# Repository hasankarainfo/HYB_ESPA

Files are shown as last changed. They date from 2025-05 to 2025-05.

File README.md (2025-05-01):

# HYB_ESPA CNC CONTROLLER BOARD
4 Adet Step motor bağlanabilir CNC kontrol kartı.

<p align="center">
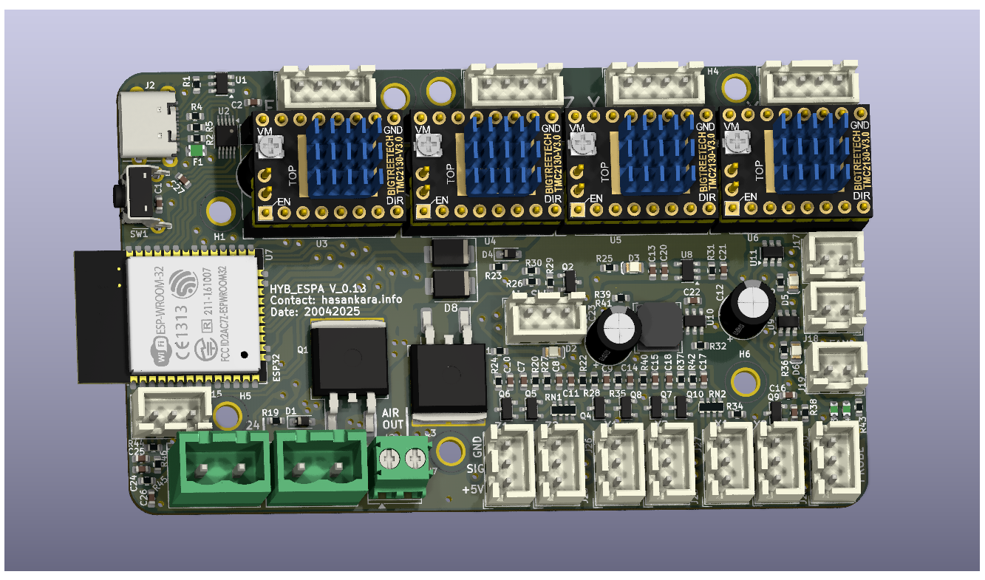
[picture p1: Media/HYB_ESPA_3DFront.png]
HYB_ESPA CNC Controller Board Readme
    
</p>
<p align="center"> Tasarım Ön Görünüm</p>
<p align="center">   
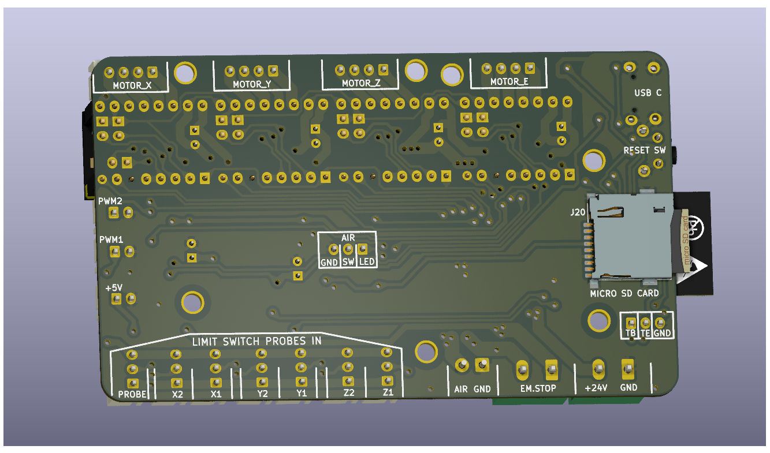
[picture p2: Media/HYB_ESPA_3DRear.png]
HYB_ESPA CNC Controller Board Readme
    
</p>
<p align="center"> Tasarım Arka Görünüm </p>

### ESP32 ile tasarlanmış cnc kontrolcü kartlarına genel bakış;

Temelde donanımsal olarak iki farklı yapıda görmek mümkün. 
İlki daha sade olan (ESPA), doğrudan mcu pinleri ile çevresel bileşen bağlantılandırılmış. 
İkincisi ise (ESPE), bazı bileşenlerin çıkış gpio ihtiyaçları için hc595 entegreleri kullanılıyor olması.

FYSETC_E4, Hem marlin hem fluidnc hem grbl firmware yazılımlarıyla uyumlu hemde açık kaynak paylaşılan projeden şematik olarak faydalanmak mümkün.
Altium ile geliştirilen proje açık kaynak paylaşılmıştır. 4 Adet TMC2209 dahili olarak step sürücüleri üzerinde barındırıyor. 
Sürücü uart bağlantıları ve uart donanımsal adreslemesini kullanmaktadır.

MKS-TinyBee, firmware yazılımları ile yine fazlaca uyumlu, yalnız kaynak tasarım olarak açık da yalnızca pdf bulunuyor. GPIO genişleme yapısı kullanılıyor. 
5 adet motor sürücü için 2* dip-8 header standart pololu breakout yapısı kullanılarak esnek motor sürücü bağlantı seçeneği sunmakta. 
yalnız TMC2208 ve ..09 için uart bağlantısı göz ardı edilmiş. Step sürücü header pinlerindeki RST ve SLP pinleri doğrudan kısa devre edili olmaktadır.

MRR_ESPE kicad ile tasarlanmış ve açık kaynak olarak paylaşılmış, tinybee ile yapısal olarak ve mcu pin görevleri olarak fazlaca benzerliği bulunan bir proje.
ek olarak SPI uyumlu step sürücüler ile haberleşmeli kullanılabilmesi için jumper seçenekleri sunmakta. 

Step sürücü header pinlerindeki MS1, MS2, MS3, RST jumper ile kontrol edilebilirken RST ve SLP pinleri de hem jumper ile kısa devre yapılaibliyor hemde kısa devre kaldırılıp mcu ya bağlanabiliyor. Özellikle TMC2208 ve ..09 uart haberleşmesi için MS3->TX ve SLP->RX olarak kullanılabileceği için gerekli esneklikler sağlanmış olmakta. 

MRR_ESPA ise yine açık kaynak paylaşılmış gpio genişleme kullanılmayan versiyonu olarak düşünülebilir.

Uart haberleşmeli step motor sürücüleri, çoğu kontrolcüye etkili düzeyde avantaj sağlamaktadır. 
Her sürücü Uart haberleşmesi için ayrıca mcu ya bağlamak fazlaca gpio kullanımı gerektirebilir.
ESP32 nin kısıtlı pin durumu için bu bir problem haline gelir. Bu sebeple Tek bir sürücüyü hem rx hem tx ile mcu bağlayıp, tüm sürücülerin sadece rx pinlerini paralel bağlamak kısmen çözüm olabiliyor.

Toplamda 2 pin gpio kullanılarak tüm sürücülere komut gönderimi mümkün olabiliyor, özellikle mod geçişleri, eşik değerleri, akım limiti microstep gibi değerlerin güncellenmesi mümkün olur.
TMC2209 uart adresleme özelliği bulunur iken TMC2208 bu özelliği desteklemez ve adres farketmeksizin tüm komutlara geri bildirim göndermektedir.
TMC2209 step motor limit switch özelliği barındırır, TMC2208 bu özellik yine bulunmamaktadır.
TMC2209 Uart adreslemesi için MS1 ve MS2 pinlerini kullanır, farklı adreslenerek uart bağlantısı paralellenmiş TMC2209 sürücüleri ile birebir haberleşme mümkün olur. 

Tek uart bağlantısı ile çoklu TMC2208 haberleşmesi kısmen mümkün olabilmektedir. Sürücülerin hepsi rx özelliği aktif iken, yalnızca birisi tx yapabilecek donanım yapısı kurgulandığında tüm sürücülere aynı parametre yükleme başarılı olmaktadır.

Açık kaynak paylaşımlar incelendiğinde esnek ve sade yapısı ile FYSETC_E4 projesi dikkat çekmektedir. 

Kendi tasarımımızı şekillendirirken özellikle gpio numara görev atamalarında ve step motor sürücü sayısında FYSETC_E4 esinlenmiş olduk.

### Tasarıma ilişkin;
1. Step motor sürücüleri pololu breakout pin yapısına uyumlu tasarlanarak, farklı step motor sürücülerine uyumluluk sağlandı. 
2. TMC2208 sürücüleri ile kullanıldığında uart üzerinden parametre yüklenebilir iken, TMC2209 ile UART RX-TX jumper takılarak, ve sürücülerde MS1, MS2 jumper configurasyonu ile uart adreslemeli kullanılabilirlik sağlandı.
3. +24V giriş voltajı ve P-mos yapısında ters bağlantı koruma özelliği eklendi.
4. Air out çıkışı ile, 42A akım değerinde ki P-mos ile Denetleyiciden kontrol edilen güçlü bir çıkış elde edildi. 24V ile beslenen lazer yada spindle doğrudan bu terminalden beslenebilir.
5. Emergency Switch terminal ile, step motor beslemesi ve Air out çıkışı, kontrolcüden bağımsız olarak kesilebilir. Kontrolcü beslemesi ve 5V hattı enerjisi aktif devam eder.
6. 5V fan çıkışı, USB ve LimitSwitch enerji hatları bağımsız PTC sigortaları ile akım korumaları eklendi.
7. Limit switch girişleri x,y ve z eksenleri için çiftlendi, aynı eksene iki farklı limit switch eklenebilir. Limit switch bağlantısı koparsa algılayabilir. Kullanılmayan giriş gnd jumper bağlanmalıdır.
8. Boot için kullanılan gpio 0 Probe bağlantısı için de kullanılmaya başlandı. ESP32 e kod atmak için Probe pini 5v jumperda iken kart resetlenerek başlatılmalıdır.
9. Tasarım aracı olarak Kicad 9 kullanıldı.

###  Layout tarafında;
1. Arduino mega2560 fiziksel boyutlarından esinlenerek 60x100 mm^2 ile alternatif cnc kontrolcü kartlarına kıyasla daha küçük ve sade yapıda tasarlandı.
2. Çift yüz tasarım yapılırken, yalnız 0.8mm delikli vialar kullanıldı. THT komponentler yalnızca arka katmandan bağlantılandı. 
3. Komponentlerin altında via bırakılmayarak kendin yap pcb üretim teknikleri ile üretim mümkün kılındı.
4. 40x40 fan doğrudan pcb üzerine distanslar ile sabitlenebilecek şekilde M3 vida delikleri yerleştirildi.

### ÜRETİM
Profesyonel pcb üretimi için; Plot klasörü içerisinde gerber ve drill dosyaları oluşturuldu.

Kendin yap seçeneği ile pcb üretimi için;
1. Plot_DIY klasörü içerisinde pcb delim için 0.8, 0.9, 1.2, 1.4, 3 mm kalınlıklarında matkap uçlarında farklı gcode lar oluşturuldu.
2. PCB komponent lehimleme işlemi için, F_Paste lazer kesim dosyası ayrıca oluşturuldu. Standart etiket kağıdına kesim yapılabilmektedir.
3. Ön yüz ve Arka yüz lazer kazıma ve hizalaması için gerekli dosyalar oluşturuldu.
4. ESP32 montajlanırken kullanılmayan pinler kapton bant ile izolasyon sağlanmalıdır.
5. ibom klasörü içerisinde html uzantılı web browser da görüntülemek üzere bom dosyası oluşturuldu. Komponent yerleşim ve dizgisinde kullanılabilmektedir.
6. Tüm lazer cnc üretim dosyaları 30W optik gücünde ki lazer makinasına göre kurgulanmıştır. Güç oranlaması ile farklı güçte ki lazer makinalarına uygunlaştırılabilir.

### 0.1b versiyon kendin yap teknikleri ile üretilmiş prototiplere ilişkin görseller
<p align="center">   
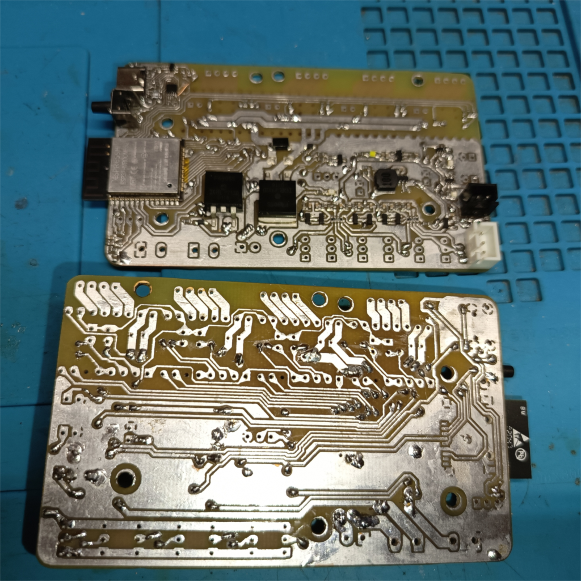
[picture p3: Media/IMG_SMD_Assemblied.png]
    
</p>
<p align="center">SMD Dizgili Ön ve Arka Görünüm </p>

<p align="center">   
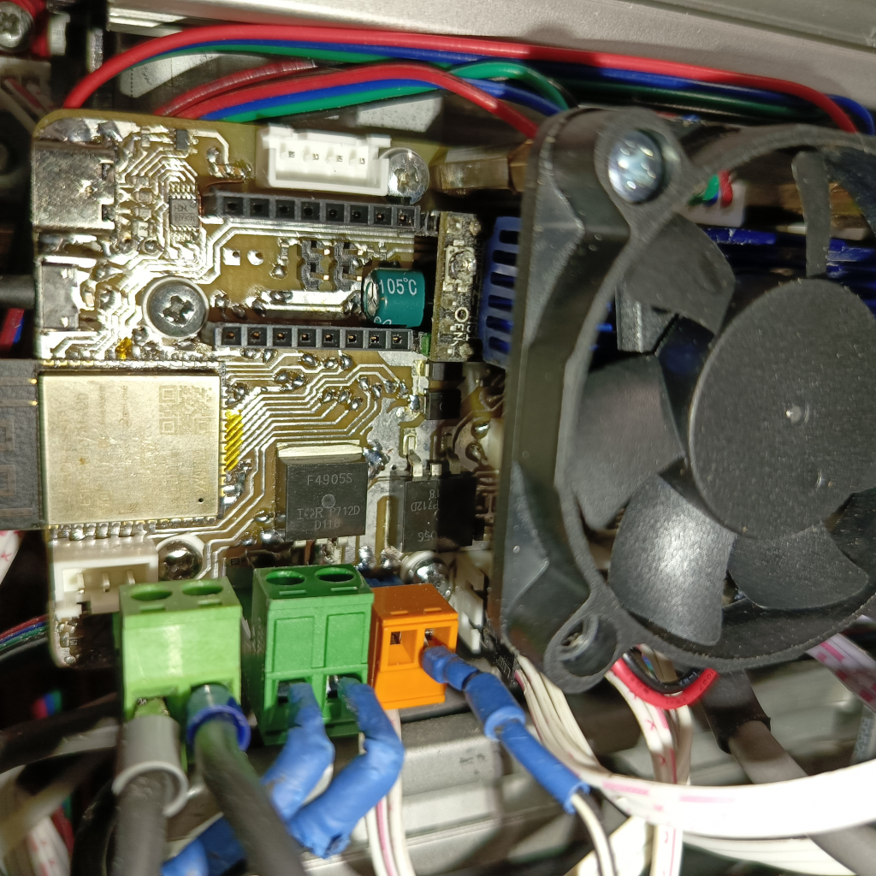
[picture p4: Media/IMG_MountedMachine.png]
    
</p>
<p align="center">Tam Dizgili ve Makine Montajlanmış Görünüm </p>

İlk prototipleme ile birlikte küçük çaplı düzeltmeler tasarımda ve üretim dosyalarında güncellenmiş (v0.1) haldedir.

Bom list oluşturulurken Türkiye piyasasından temin edilmek üzere ürün linkleri oluşturuldu. Yalnız CH340E IC yerli piyasada bulunamadı. 
Belirtilen fiyat bilgileri için ise, vergiler dahil edildi, güncel dolar kuru esas alındı ve dolara çevrildi.

### Bazı testlere ilişkin;
1. Firmware olarak fluidnc v3.9.4 yüklendi. Kontrolcüyle uyumlu, oluşturulan config.yaml dosyası "Settings/" dizini içerisine yerleştirildi.
2. X, Y ve Z eksenleri için 3 adet TMC2208 step motor sürücüleri bağlandı. Tüm sürücülere parametre yükleme yapılabildiği teyit edildi.
3. Arayüz olarak UGS (version 2.1.12) ile bağlanarak temel testler başarıyla sağlandı. 
4. Fiziksel SD kart takılarak web arayüz üzerinden .gcode yüklendi ve ilgili gcode çalıştırıldı. 
5. AirOut çıkışına fiziksel röle bağlandı ve röle çıkışına spindle 220V beslemesi bağlandı.
6. Fluidnc config ayarlarında AirOut çıkışı pwm enable pini ile ilişkilendirildi. 
7. M3 komutu çalıştırılarak Spindle enerjisi sağlandı, M5 komutu çalıştırıldığında Spindle enerjisi otomatik kesildi.
8. Pwm çıkışı ile spindle motor hız ayarı çalıştırıldı.
9. Kontrolcü spindle için enerji çıkışı sağlarken de acil stop basıldığında, spindle enerjisi doğrudan kesilebildi.
10. Limit switch kablo temassızlığı algılanabildiği görüldü.

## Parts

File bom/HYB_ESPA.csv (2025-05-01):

 | Sourced | Placed | References | Value | Part Number | Part Link | Price | Quantity
1 |  |  | C1, C7, C8, C9, C10, C11, C14, C15, C16, C17, C18, C19 | 1nF | CL10B102KB8NNNC | https://ozdisan.com/Product/Detail/11971/CL10B102KB8NNNC | 0.006 | 12
2 |  |  | C2, C13, C21, C22, C25, C27 | 100nF | CC0603KRX7R9BB104 | https://ozdisan.com/Product/Detail/476015/CC0603KRX7R9BB104 | 0.006 | 6
3 |  |  | C3, C4, C5, C6, C12 | 220uF 25V | TMP221M1EE11M | https://ozdisan.com/Product/Detail/404352/TMP221M1EE11M | 0.06 | 5
4 |  |  | C24, C26 | 2.2uF | CL10A225KQ8NNNC | https://www.ozdisan.com/Product/Detail/401994/CL10A225KQ8NNNC | 0.01 | 2
5 |  |  | C20 | 22uF 6.3V | CL10A226MQ8NRNC | https://ozdisan.com/Product/Detail/431703/CL10A226MQ8NRNC | 0.038 | 1
6 |  |  | C23 | 470uF 10V | PKLH-010V471ME110-T2.5 | https://ozdisan.com/Product/Detail/1046555/PKLH-010V471ME110-T2-5 | 0.05 | 1
7 |  |  | R6, R8, R10, R11, R13, R14, R15, R18, R20, R22, R24, R27, R28, R34, R35, R37, R38, R40, R42 | 10K | 0603SAF1002T5E | https://ozdisan.com/Product/Detail/341790/0603SAF1002T5E | 0.0015 | 19
8 |  |  | R1, R2, R7, R9, R12, R16, R21, R26, R30, R31, R44, R45, R46 | 4.7K | RC0603FR-074K7L | https://ozdisan.com/Product/Detail/494590/RC0603FR-074K7L | 0.0018 | 13
9 |  |  | R19, R23, R29, R32 | 100K | 0603SAF1003T5E | https://ozdisan.com/Product/Detail/339374/0603SAF1003T5E | 0.0015 | 4
10 |  |  | R25, R33, R36 | 1K | 0603SAF1001T5E | https://ozdisan.com/Product/Detail/341789/0603SAF1001T5E | 0.0015 | 3
11 |  |  | R4, R5 | 10R | CQ03SAF100JT5E | https://ozdisan.com/Product/Detail/587941/CQ03SAF100JT5E | 0.002 | 2
12 |  |  | R17 | 100R | 0603SAF1000T5E | https://ozdisan.com/Product/Detail/341784/0603SAF1000T5E | 0.0015 | 1
13 |  |  | R39 | 3K | 0603SAF3001T5E | https://ozdisan.com/Product/Detail/339378/0603SAF3001T5E | 0.0015 | 1
14 |  |  | R41 | 16K | 0603SAF1602T5E | https://ozdisan.com/Product/Detail/359801/0603SAF1602T5E | 0.0015 | 1
15 |  |  | R43 | 0R | 0603SAF0000T5E | https://ozdisan.com/Product/Detail/352049/0603SAF0000T5E | 0.0015 | 1
16 |  |  | L1 | 10uH 2.25A | NR6028-100M | https://ozdisan.com/Product/Detail/529366/NR6028-100M | 0.16 | 1
17 |  |  | D2, D3, D5, D6 | LedAir, Led3V3, LedPWM2, LedPWM | HL-PSC-2012H233W-HF4 | https://ozdisan.com/Product/Detail/490003/HL-PSC-2012H233W-HF4 | 0.024 | 4
18 |  |  | D1, D4 | MM3Z12 | MM3Z12-HT | https://ozdisan.com/Product/Detail/581368/MM3Z12-HT | 0.025 | 2
19 |  |  | D7, D8 | SMBJ26CA | SMBJ26CA-HT | https://ozdisan.com/Product/Detail/503708/SMBJ26CA-HT | 0.1 | 2
20 |  |  | U3, U4, U5, U6 | Stepper Breakout | MSK.STP.01.000018 | https://www.motorobit.com/tmc2209-v20-step-motor-surucusu | 6.4 | 4
21 |  |  | U9, U11 | SN74LVC1T45DBV | SN74LVC1T45DBVT | https://ozdisan.com/Product/Detail/616843/SN74LVC1T45DBVT | 0.7 | 2
22 |  |  | U1 | SMF05CT1G | SMF05CT1G | https://www.ozdisan.com/Product/Detail/575537/SMF05CT1G | 0.18 | 1
23 |  |  | U2 | CH340E | C99652 | https://www.lcsc.com/product-detail/USB-ICs_WCH-Jiangsu-Qin-Heng-CH340E_C99652.html | 0.55 | 1
24 |  |  | U7 | ESP32 | ESP32-WROOM-32UE-N4.ESP | https://www.empastore.com/esp32-wroom-32ue-n4-wifi-bluetooth-modul | 3.45 | 1
25 |  |  | U8 | AP7366 | AP7366EA-33W5-7 | https://www.digikey.com/en/products/detail/diodes-incorporated/AP7366EA-33W5-7/18635685 | 0.138 | 1
26 |  |  | U10 | AP63201 | AP63201WU-7 | https://ozdisan.com/Product/Detail/1060556/AP63201WU-7 | 0.4 | 1
27 |  |  | F3, F4 | 100mA 15V | FSMD010-0603-R | https://ozdisan.com/Product/Detail/470708/FSMD010-0603-R | 0.1 | 2
28 |  |  | F1 | 1.1A 6V | KLM2S110RY | https://ozdisan.com/Product/Detail/490835/KLM2S110RY | 0.085 | 1
29 |  |  | SW1 | SW_Reset | L-KLS7-TS6606-5.0-180 | https://ozdisan.com/Product/Detail/462867/L-KLS7-TS6606-5-0-180 | 0.08 | 1
30 |  |  | Q2, Q4, Q5, Q6, Q7, Q8, Q9, Q10 | PJA3440 | PJA3440_R2_00001 | https://ozdisan.com/Product/Detail/517995/PJA3440R200001 | 0.1 | 8
31 |  |  | Q1, Q3 | IRF4905 | IRF4905STRLPBF | https://ozdisan.com/Product/Detail/612241/IRF4905STRLPBF | 1.3 | 2
32 |  |  | RN1, RN2 | 1K | 4D03WGF1001T5E | https://ozdisan.com/Product/Detail/423589/4D03WGF1001T5E | 0.017 | 2
33 |  |  | J4, J5, J7, J8, J10, J11, J12, J14, J31 | E_J2, E_J1, Z_J1, Z_J2, Y_J1, X_J1, Y_J2, X_J2, UART | DS1069-2MVW6X | https://ozdisan.com/Product/Detail/347994/DS1069-2MVW6X | 0.01 | 9
34 |  |  | J15, J16, J24, J25, J26, J27, J28, J29, J30 | AnIn, AirSW, Z_LIM1, Z_LIM2, Y_LIM1, X_LIM1, Y_LIM2, X_LIM2, Probe | L-KLS1-2.50-03-S | https://ozdisan.com/Product/Detail/456067/L-KLS1-2-50-03-S | 0.018 | 9
35 |  |  | J3, J6, J9, J13 | E_Stepper, Z_Stepper, X_Stepper, Y_Stepper | DS1069-4MVW6X | https://ozdisan.com/Product/Detail/347998/DS1069-4MVW6X | 0.02 | 4
36 |  |  | J17, J18, J19 | PWM2_Drive, 5V FAN | DS1069-2MVW6X | https://ozdisan.com/Product/Detail/347994/DS1069-2MVW6X | 0.01 | 3
37 |  |  | J21, J23 | PowerIn, EmStop | ZB2EDGV-5.08-2P | https://ozdisan.com/Product/Detail/1042573/ZB2EDGV-5-08-2P | 0.045 | 2
38 |  |  | J2 | USB_C | nc | https://robiz.net/typec16pin?search=type-c&description=true | 0.2 | 1
39 |  |  | J20 | Micro_SD_Card_Det1 | 112I-TA01 | https://ozdisan.com/Product/Detail/637838/112I-TA01 | 1 | 1
40 |  |  | J22 | AirOut | 15EDGVC-3.5-02P-12-00AH | https://ozdisan.com/Product/Detail/707708/15EDGVC-3-5-02P-12-00AH | 0.1 | 1

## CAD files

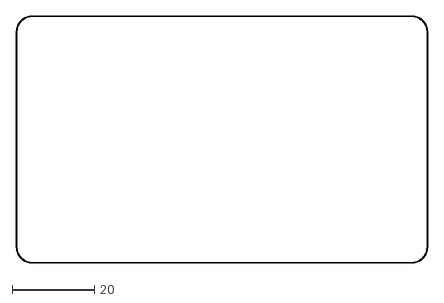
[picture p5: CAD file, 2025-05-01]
Plot_DIY/HYB_ESPA-Edge_Cuts.dxf
100.1 x 60.1

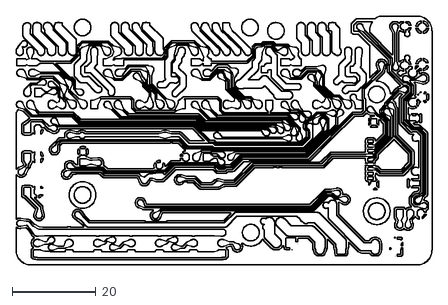
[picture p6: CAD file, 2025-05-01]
Plot_DIY/HYB_ESPA-B_Cu_mirror.DXF
99.4 x 59.4

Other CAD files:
Plot_DIY/HYB_ESPA-F_Paste.dxf

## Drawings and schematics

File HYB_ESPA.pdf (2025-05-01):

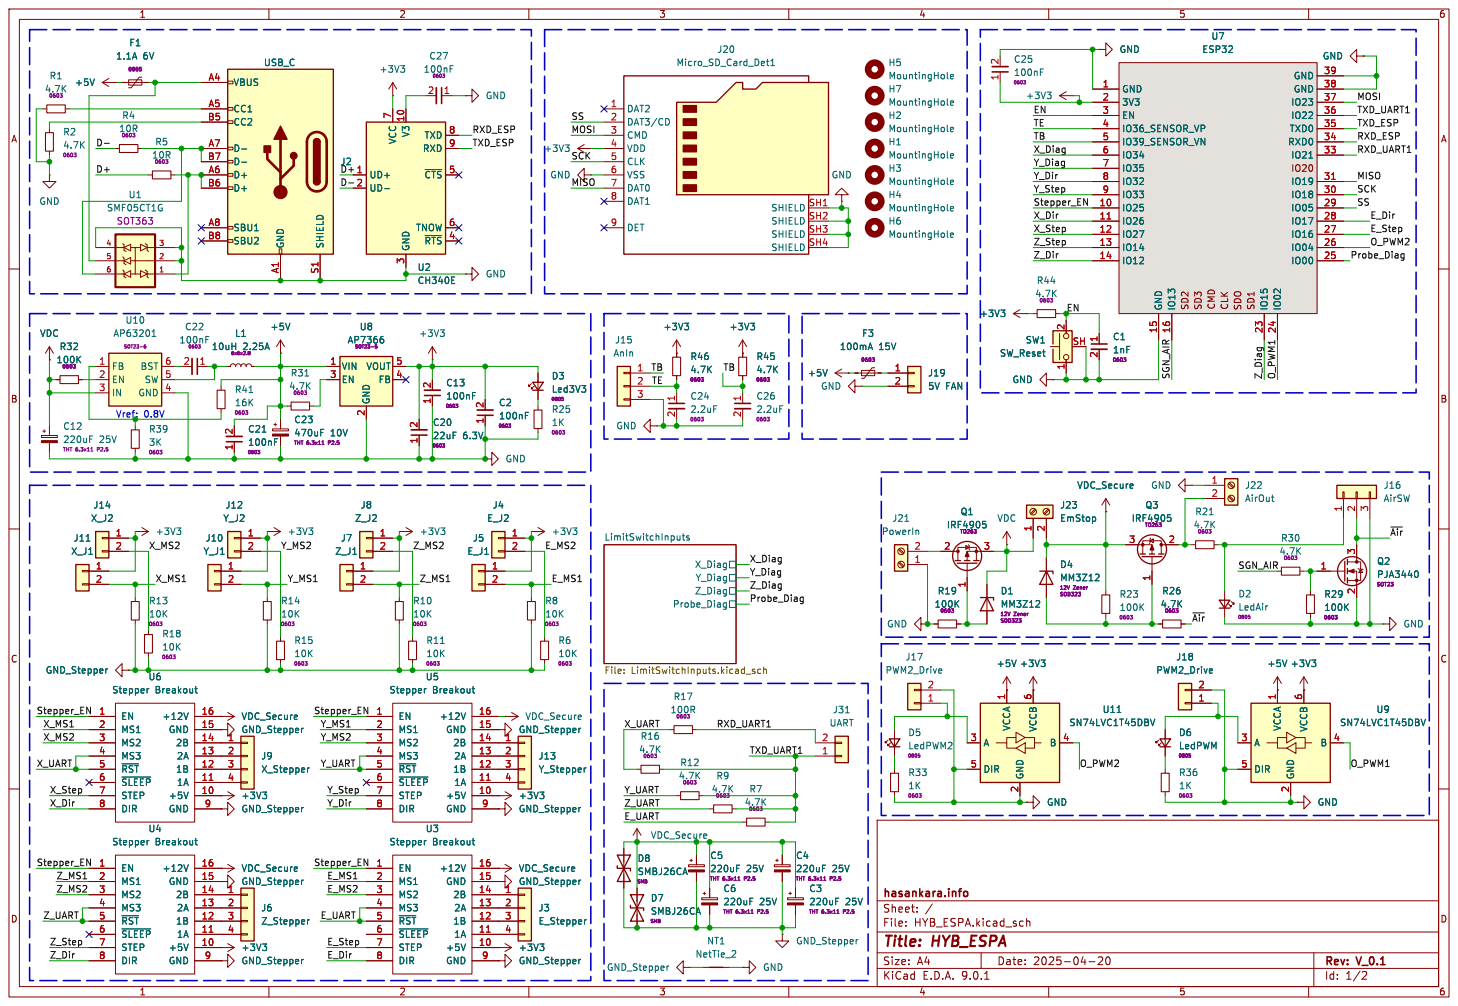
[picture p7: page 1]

3 TXD 8 RXD 9 ~{CTS}5 TNOW 6 ~{RTS}4 U2 CH340E SHIELD S1 GND A1 VBUS A4 CC1 A5 CC2 B5 D- A7 D- B7 D+ A6 D+ B6 SBU1 A8 SBU2 B8

3 TXD 8 RXD 9 ~{CTS}5 TNOW 6 ~{RTS}4

File: HYB_ESPA.kicad_sch Sheet: / hasankara.info

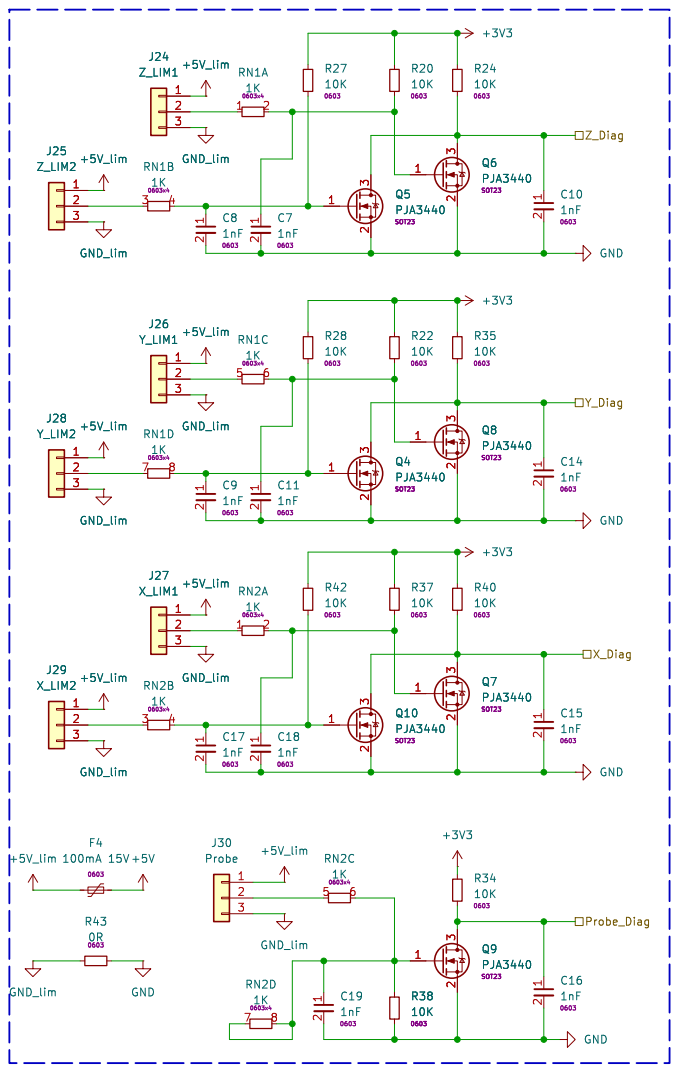
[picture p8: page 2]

File: LimitSwitchInputs.kicad_sch Sheet: /LimitSwitchInputs/ hasankara.info

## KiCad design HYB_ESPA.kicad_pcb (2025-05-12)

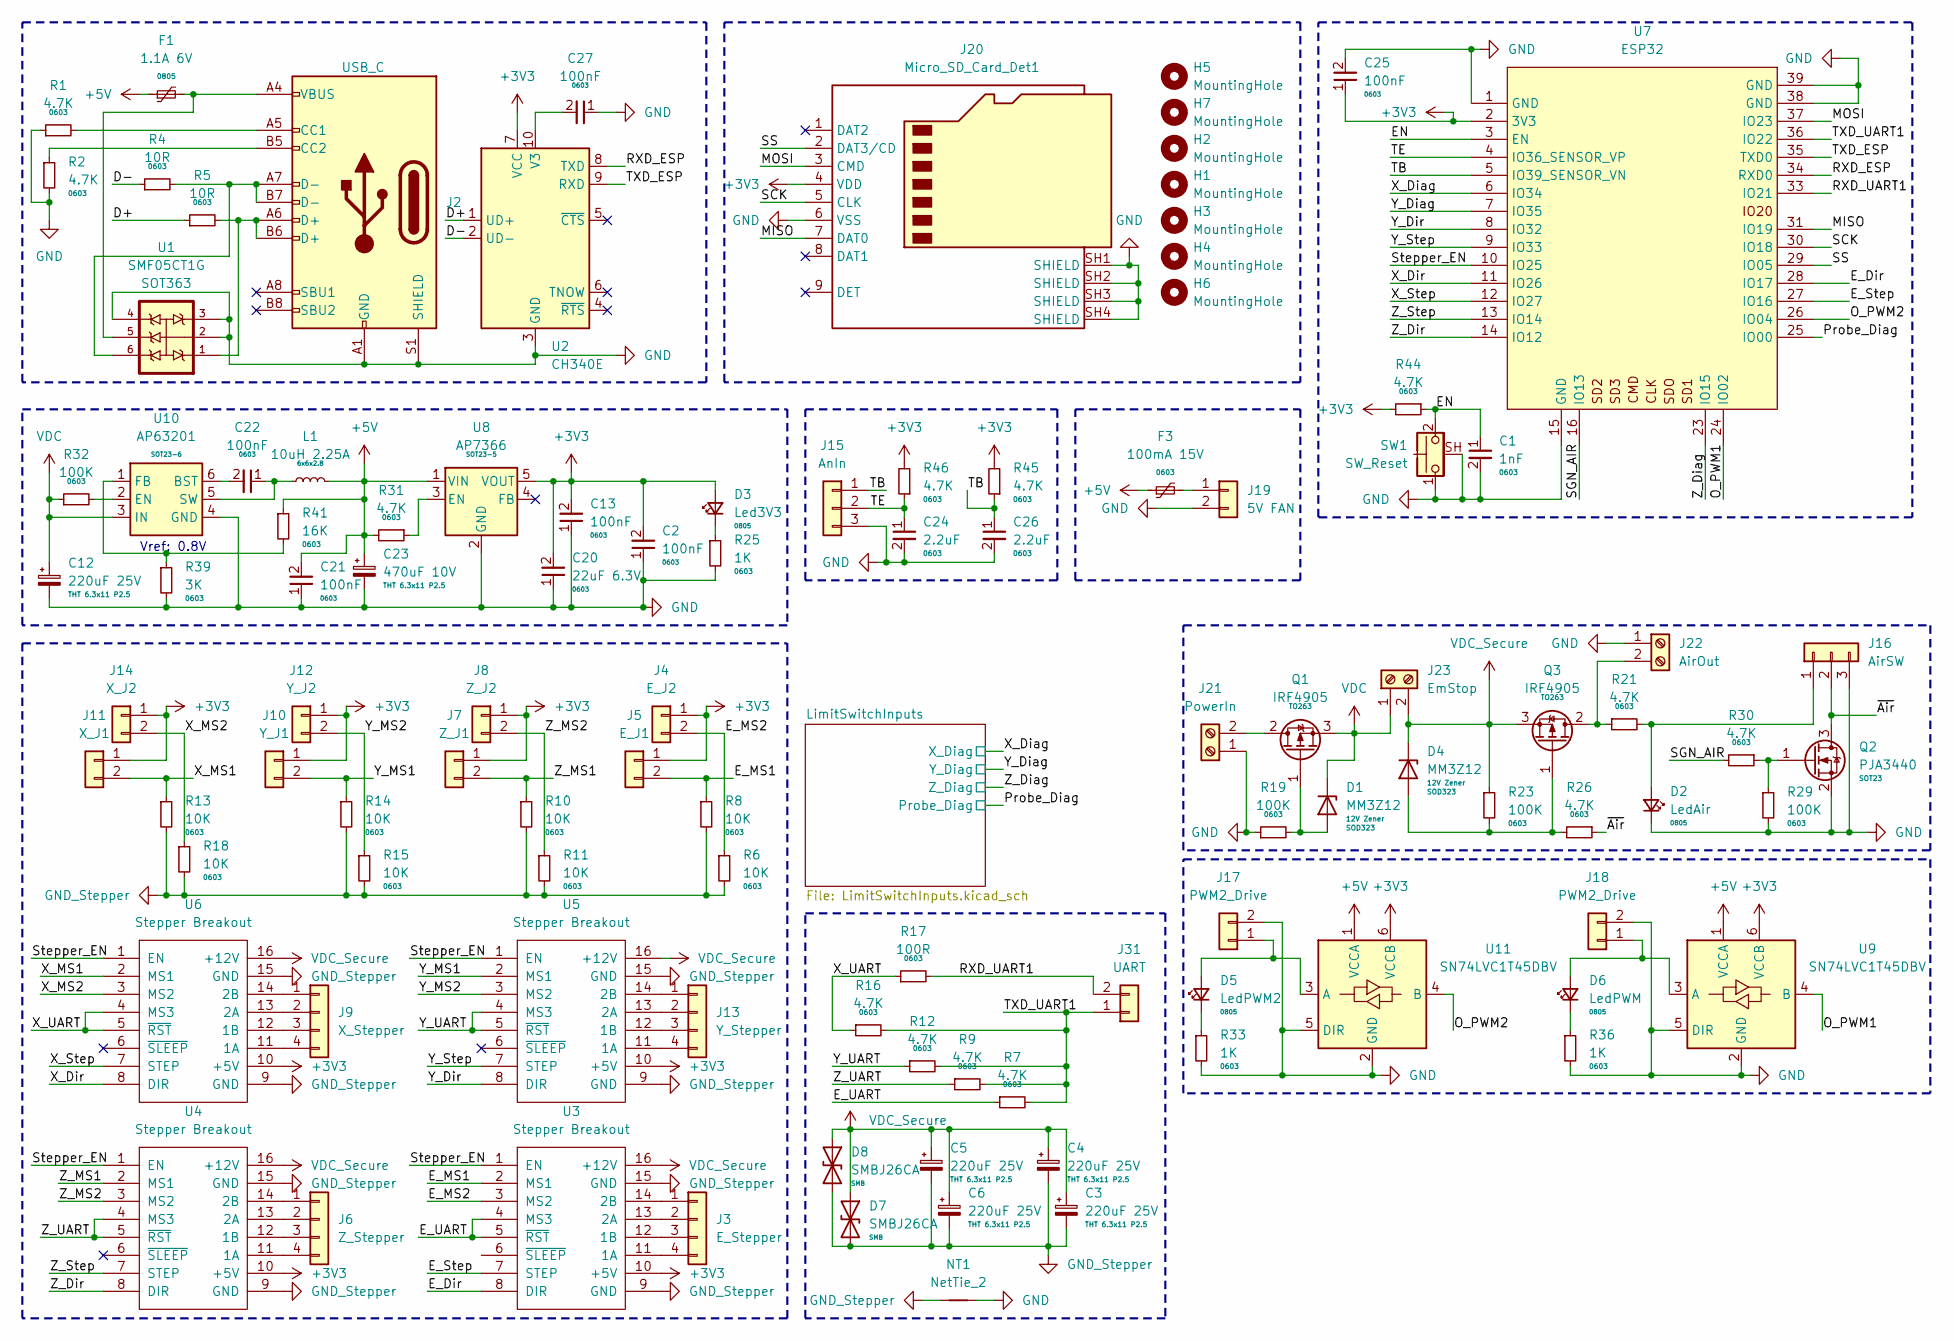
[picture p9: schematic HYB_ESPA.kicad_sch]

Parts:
C1: 1nF; C_0603_1608Metric; Part Number CL10B102KB8NNNC
C2, C13, C21, C22, C25, C27: 100nF; C_0603_1608Metric_SlimPad; Part Number CC0603KRX7R9BB104
C3, C4, C5, C6, C12: 220uF 25V; CP_Radial_D6.3mm_H11.0mm_P2.50mm; Part Number TMP221M1EE11M
C20: 22uF 6.3V; C_0603_1608Metric; Part Number CL10A226MQ8NRNC
C23: 470uF 10V; CP_Radial_D6.3mm_H11.0mm_P2.50mm; Part Number PKLH-010V471ME110-T2.5
C24, C26: 2.2uF; C_0603_1608Metric_SlimPad; Part Number CL10A225KQ8NNNC
D1, D4: MM3Z12; D_SOD-323_HandSoldering; Part Number MM3Z12-HT
D2: LedAir; LED_0805_2012Metric-s; Part Number HL-PSC-2012H233W-HF4
D3: Led3V3; LED_0805_2012Metric-s; Part Number HL-PSC-2012H233W-HF4
D5: LedPWM2; LED_0805_2012Metric-s; Part Number HL-PSC-2012H233W-HF4
D6: LedPWM; LED_0805_2012Metric-s; Part Number HL-PSC-2012H233W-HF4
D7, D8: SMBJ26CA; D_SMB_SmallPad; Part Number SMBJ26CA-HT
F1: 1.1A 6V; Fuse_0805_2012Metric; Part Number KLM2S110RY
F3: 100mA 15V; Fuse_0603_1608Metric; Part Number FSMD010-0603-R
H1, H2, H3, H4, H5, H6, H7: MountingHole; MountingHole_3.2mm_M3_DIN965_SmallPad
J2: USB_C; USB_C_Receptacle_GCT_USB4105-xx-A_16P_TopMnt_Horizontal_SPEC; Part Number nc
J3: E_Stepper; JST_XH_B4B-XH-A_1x04_P2.50mm_Vertical; Part Number DS1069-4MVW6X
J4: E_J2; PinHeader_1x02_P2.54mm_Vertical_1L; Part Number DS1069-2MVW6X
J5: E_J1; PinHeader_1x02_P2.54mm_Vertical_1L; Part Number DS1069-2MVW6X
J6: Z_Stepper; JST_XH_B4B-XH-A_1x04_P2.50mm_Vertical; Part Number DS1069-4MVW6X
J7: Z_J1; PinHeader_1x02_P2.54mm_Vertical_1L; Part Number DS1069-2MVW6X
J8: Z_J2; PinHeader_1x02_P2.54mm_Vertical_1L; Part Number DS1069-2MVW6X
J9: X_Stepper; JST_XH_B4B-XH-A_1x04_P2.50mm_Vertical; Part Number DS1069-4MVW6X
J10: Y_J1; PinHeader_1x02_P2.54mm_Vertical_1L; Part Number DS1069-2MVW6X
J11: X_J1; PinHeader_1x02_P2.54mm_Vertical_1L; Part Number DS1069-2MVW6X
J12: Y_J2; PinHeader_1x02_P2.54mm_Vertical_1L; Part Number DS1069-2MVW6X
J13: Y_Stepper; JST_XH_B4B-XH-A_1x04_P2.50mm_Vertical; Part Number DS1069-4MVW6X
J14: X_J2; PinHeader_1x02_P2.54mm_Vertical_1L; Part Number DS1069-2MVW6X
J15: AnIn; JST_XH_B3B-XH-A_1x03_P2.50mm_Vertical; Part Number L-KLS1-2.50-03-S
J16: AirSW; JST_XH_B3B-XH-A_1x03_P2.50mm_Vertical; Part Number L-KLS1-2.50-03-S
J17, J18: PWM2_Drive; JST_XH_B2B-XH-A_1x02_P2.50mm_Vertical; Part Number DS1069-2MVW6X
J19: 5V FAN; JST_XH_B2B-XH-A_1x02_P2.50mm_Vertical; Part Number DS1069-2MVW6X
J20: Micro_SD_Card_Det1; MicroSD_Card_Holder; Part Number 112I-TA01
J21: PowerIn; PhoenixContact_MSTBVA_2,5_2-G-5,08_1x02_P5.08mm_Vertical; Part Number ZB2EDGV-5.08-2P
J22: AirOut; TerminalBlock_Phoenix_PT-1,5-2-3.5-H_1x02_P3.50mm_Horizontal; Part Number 15EDGVC-3.5-02P-12-00AH
J23: EmStop; PhoenixContact_MSTBVA_2,5_2-G-5,08_1x02_P5.08mm_Vertical; Part Number ZB2EDGV-5.08-2P
J31: UART; PinHeader_1x02_P2.54mm_Vertical_1L; Part Number DS1069-2MVW6X
L1: 10uH 2.25A; L_CoreMaster_NR6028; Part Number NR6028-100M
NT1: NetTie_2; NetTie-2_SMD_Pad2.0mm
Q1, Q3: IRF4905; TO-263-2-S; Part Number IRF4905STRLPBF
Q2: PJA3440; SOT-23-3-s; Part Number PJA3440_R2_00001
R1, R2, R7, R9, R12, R16, R21, R26, R30, R31, R44, R45, R46: 4.7K; R_0603_1608Metric; Part Number RC0603FR-074K7L
R4, R5: 10R; R_0603_1608Metric; Part Number CQ03SAF100JT5E
R6, R8, R10, R11, R13, R14, R15, R18: 10K; R_0603_1608Metric; Part Number 0603SAF1002T5E
R17: 100R; R_0603_1608Metric; Part Number 0603SAF1000T5E
R19, R23, R29, R32: 100K; R_0603_1608Metric; Part Number 0603SAF1003T5E
R25, R33, R36: 1K; R_0603_1608Metric; Part Number 0603SAF1001T5E
R39: 3K; R_0603_1608Metric; Part Number 0603SAF3001T5E
R41: 16K; R_0603_1608Metric; Part Number 0603SAF1602T5E
SW1: SW_Reset; SW_Tactile_SPST_Angled_PTS645Vx39-2LFS_Shielded; Part Number L-KLS7-TS6606-5.0-180
U1: SMF05CT1G; TSOT-23-6_SlimPad; Part Number SMF05CT1G
U2: CH340E; MSOP-10_3x3mm_P0.5mm_SlimPad; Part Number C99652
U3, U4, U5, U6: Stepper Breakout; Pololu_Breakout-16_15.2x20.3mm_TMC; Part Number MSK.STP.01.000018
U7: ESP32; ESP32_WROOM_SIMPLE; Part Number ESP32-WROOM-32UE-N4.ESP
U8: AP7366; TSOT-23-5; Part Number AP7366EA-33W5-7
U9, U11: SN74LVC1T45DBV; SOT-23-6; Part Number SN74LVC1T45DBVT
U10: AP63201; TSOT-23-6_SlimPad; Part Number AP63201WU-7

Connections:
+3V3: C2.2, C13.2, C20.2, C25.1, D3.2 (A), J4.1, J5.1, J7.1, J8.1, J10.1, J11.1, J12.1, J14.1, J20.4 (VDD), R44.2, R45.2, R46.2, U2.7 (VCC), U3.10 (+5V), U4.10 (+5V), U5.10 (+5V), U6.10 (+5V), U7.2 (3V3), U8.5 (VOUT), U9.6 (VCCB), U11.6 (VCCB); also elsewhere on the board
+5V: C21.2, C23.1, F1.1, F3.1, L1.1, R31.2, R41.1, U8.1 (VIN), U9.1 (VCCA), U11.1 (VCCA); also elsewhere on the board
/D+: R5.1, U2.1 (UD+)
/D-: R4.1, U2.2 (UD-)
/EN: C1.1, R44.1, SW1.2, U7.3 (EN)
/E_Dir: U3.8 (DIR), U7.28 (IO17)
/E_MS1: J5.2, R8.1, U3.2 (MS1)
/E_MS2: J4.2, R6.1, U3.3 (MS2)
/E_Step: U3.7 (STEP), U7.27 (IO16)
/E_UART: R7.1, U3.4 (MS3), U3.5 (~RST)
/MISO: J20.7 (DAT0), U7.31 (IO19)
/MOSI: J20.3 (CMD), U7.37 (IO23)
/O_PWM1: U7.24 (IO02), U9.4 (B)
/O_PWM2: U7.26 (IO04), U11.4 (B)
/Probe_Diag: U7.25 (IO00); also elsewhere on the board
/RXD_ESP: U2.8 (TXD), U7.34 (RXD0)
/RXD_UART1: J31.2, R17.2, U7.33 (IO21)
/SCK: J20.5 (CLK), U7.30 (IO18)
/SGN_AIR: R30.2, U7.16 (IO13)
/SS: J20.2 (DAT3/CD), U7.29 (IO05)
/Stepper_EN: U3.1 (EN), U4.1 (EN), U5.1 (EN), U6.1 (EN), U7.10 (IO25)
/TB: C26.1, J15.1, R45.1, U7.5 (IO39_SENSOR_VN)
/TE: C24.1, J15.2, R46.1, U7.4 (IO36_SENSOR_VP)
/TXD_ESP: U2.9 (RXD), U7.35 (TXD0)
/TXD_UART1: J31.1, R7.2, R9.2, R12.2, R16.2, U7.36 (IO22)
/X_Diag: U7.6 (IO34); also elsewhere on the board
/X_Dir: U6.8 (DIR), U7.11 (IO26)
/X_MS1: J11.2, R13.1, U6.2 (MS1)
/X_MS2: J14.2, R18.1, U6.3 (MS2)
/X_Step: U6.7 (STEP), U7.12 (IO27)
/X_UART: R16.1, R17.1, U6.4 (MS3), U6.5 (~RST)
/Y_Diag: U7.7 (IO35); also elsewhere on the board
/Y_Dir: U5.8 (DIR), U7.8 (IO32)
/Y_MS1: J10.2, R14.1, U5.2 (MS1)
/Y_MS2: J12.2, R15.1, U5.3 (MS2)
/Y_Step: U5.7 (STEP), U7.9 (IO33)
/Y_UART: R12.1, U5.4 (MS3), U5.5 (~RST)
/Z_Diag: U7.23 (IO15); also elsewhere on the board
/Z_Dir: U4.8 (DIR), U7.14 (IO12)
/Z_MS1: J7.2, R10.1, U4.2 (MS1)
/Z_MS2: J8.2, R11.1, U4.3 (MS2)
/Z_Step: U4.7 (STEP), U7.13 (IO14)
/Z_UART: R9.1, U4.4 (MS3), U4.5 (~RST)
/~Air: J16.2, Q2.3 (D), R26.1
GND: C1.2, C2.1, C12.2, C13.1, C20.1, C21.1, C23.2, C24.2, C25.2, C26.2, C27.1, D2.1 (K), J2.A1 (GND), J2.A12 (GND), J2.B1 (GND), J2.B12 (GND), J2.S1 (SHIELD), J15.3, J16.3, J17.2, J18.2, J19.2, J20.6 (VSS), J20.SH1 (SHIELD), J20.SH2 (SHIELD), J20.SH3 (SHIELD), J20.SH4 (SHIELD), J21.1, J22.1, NT1.2, Q2.2 (S), R1.1, R2.2, R19.1, R25.2, R29.2, R33.2, R36.2, R39.2, SW1.1, SW1.SH (B), U1.2, U1.3, U1.4, U2.3 (GND), U7.1 (GND), U7.15 (GND), U7.38 (GND), U7.39 (GND), U8.2 (GND), U9.2 (GND), U9.5 (DIR), U10.4 (GND), U11.2 (GND), U11.5 (DIR); also elsewhere on the board
GND_Stepper: C3.2, C4.2, C5.2, C6.2, D7.2 (A2), D8.2 (A2), NT1.1, R6.2, R8.2, R10.2, R11.2, R13.2, R14.2, R15.2, R18.2, U3.9 (GND), U3.15 (GND), U4.9 (GND), U4.15 (GND), U5.9 (GND), U5.15 (GND), U6.9 (GND), U6.15 (GND)
unnamed: D1.2 (A), Q1.1 (G), R19.2
unnamed: D2.2 (A), J16.1, R21.2
unnamed: D3.1 (K), R25.1
unnamed: D4.2 (A), Q3.1 (G), R23.2, R26.2
unnamed: D5.2 (A), J17.1, U11.3 (A)
unnamed: D5.1 (K), R33.1
unnamed: D6.2 (A), J18.1, U9.3 (A)
unnamed: D6.1 (K), R36.1
unnamed: F1.2, J2.A4 (VBUS), J2.A9 (VBUS), J2.B4 (VBUS), J2.B9 (VBUS), U1.5
unnamed: J2.A5 (CC1), R1.2
unnamed: J2.B5 (CC2), R2.1
unnamed: J2.A6 (D+), J2.B6 (D+), R5.2, U1.1
unnamed: J2.A7 (D-), J2.B7 (D-), R4.2, U1.6
unnamed: J3.1, U3.14 (2B)
unnamed: J3.2, U3.13 (2A)
unnamed: J3.3, U3.12 (1B)
unnamed: J3.4, U3.11 (1A)
unnamed: J6.1, U4.14 (2B)
unnamed: J6.2, U4.13 (2A)
unnamed: J6.3, U4.12 (1B)
unnamed: J6.4, U4.11 (1A)
unnamed: J9.1, U6.14 (2B)
unnamed: J9.2, U6.13 (2A)
unnamed: J9.3, U6.12 (1B)
unnamed: J9.4, U6.11 (1A)
unnamed: J13.1, U5.14 (2B)
unnamed: J13.2, U5.13 (2A)
unnamed: J13.3, U5.12 (1B)
unnamed: J13.4, U5.11 (1A)
unnamed: F3.2, J19.1
unnamed: J21.2, Q1.2 (S)
unnamed: J22.2, Q3.2 (S), R21.1
unnamed: Q2.1 (G), R29.1, R30.1
unnamed: C27.2, U2.10 (V3)
unnamed: R31.1, U8.3 (EN)
unnamed: C22.2, U10.6 (BST)
unnamed: R32.2, U10.2 (EN)
unnamed: R39.1, R41.2, U10.1 (FB)
unnamed: C22.1, L1.2, U10.5 (SW)
VDC: C12.1, D1.1 (K), J23.1, Q1.3 (D), R32.1, U10.3 (IN)
VDC_Secure: C3.1, C4.1, C5.1, C6.1, D4.1 (K), D7.1 (A1), D8.1 (A1), J23.2, Q3.3 (D), R23.1, U3.16 (+12V), U4.16 (+12V), U5.16 (+12V), U6.16 (+12V)

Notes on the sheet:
Vref: 0.8V

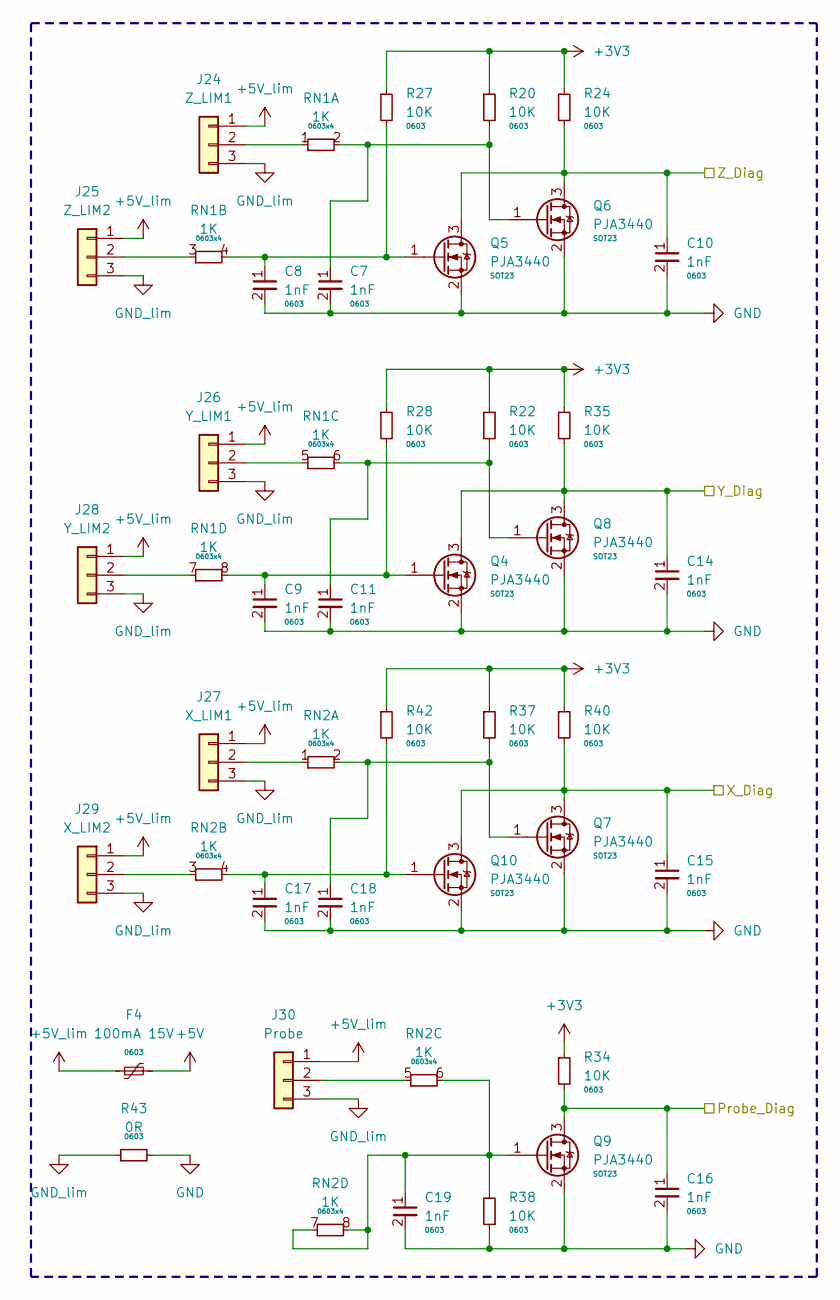
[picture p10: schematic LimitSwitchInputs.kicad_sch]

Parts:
C7, C8, C9, C10, C11, C14, C15, C16, C17, C18, C19: 1nF; C_0603_1608Metric; Part Number CL10B102KB8NNNC
F4: 100mA 15V; Fuse_0603_1608Metric; Part Number FSMD010-0603-R
J24: Z_LIM1; JST_XH_B3B-XH-A_1x03_P2.50mm_Vertical; Part Number L-KLS1-2.50-03-S
J25: Z_LIM2; JST_XH_B3B-XH-A_1x03_P2.50mm_Vertical; Part Number L-KLS1-2.50-03-S
J26: Y_LIM1; JST_XH_B3B-XH-A_1x03_P2.50mm_Vertical; Part Number L-KLS1-2.50-03-S
J27: X_LIM1; JST_XH_B3B-XH-A_1x03_P2.50mm_Vertical; Part Number L-KLS1-2.50-03-S
J28: Y_LIM2; JST_XH_B3B-XH-A_1x03_P2.50mm_Vertical; Part Number L-KLS1-2.50-03-S
J29: X_LIM2; JST_XH_B3B-XH-A_1x03_P2.50mm_Vertical; Part Number L-KLS1-2.50-03-S
J30: Probe; JST_XH_B3B-XH-A_1x03_P2.50mm_Vertical; Part Number L-KLS1-2.50-03-S
Q4, Q5, Q6, Q7, Q8, Q9, Q10: PJA3440; SOT-23-3-s; Part Number PJA3440_R2_00001
R20, R22, R24, R27, R28, R34, R35, R37, R38, R40, R42: 10K; R_0603_1608Metric; Part Number 0603SAF1002T5E
R43: 0R; R_0603_1608Metric; Part Number 0603SAF0000T5E
RN1, RN2: 1K; R_Array_Convex_4x0603-s; Part Number 4D03WGF1001T5E

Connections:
+3V3: R20.1, R22.1, R24.1, R27.1, R28.1, R34.1, R35.1, R37.1, R40.1, R42.1; also elsewhere on the board
+5V: F4.2; also elsewhere on the board
+5V_lim: F4.1, J24.1, J25.1, J26.1, J27.1, J28.1, J29.1, J30.1
/Probe_Diag: C16.1, Q9.3 (D), R34.2; also elsewhere on the board
/X_Diag: C15.1, Q7.3 (D), Q10.3 (D), R40.2; also elsewhere on the board
/Y_Diag: C14.1, Q4.3 (D), Q8.3 (D), R35.2; also elsewhere on the board
/Z_Diag: C10.1, Q5.3 (D), Q6.3 (D), R24.2; also elsewhere on the board
GND: C7.2, C8.2, C9.2, C10.2, C11.2, C14.2, C15.2, C16.2, C17.2, C18.2, C19.2, Q4.2 (S), Q5.2 (S), Q6.2 (S), Q7.2 (S), Q8.2 (S), Q9.2 (S), Q10.2 (S), R38.1, R43.2; also elsewhere on the board
GND_lim: J24.3, J25.3, J26.3, J27.3, J28.3, J29.3, J30.3, R43.1
unnamed: J24.2, RN1.1
unnamed: J25.2, RN1.3
unnamed: J26.2, RN1.5
unnamed: J27.2, RN2.1
unnamed: J28.2, RN1.7
unnamed: J29.2, RN2.3
unnamed: J30.2, RN2.5
unnamed: C9.1, Q4.1 (G), R28.2, RN1.8
unnamed: C8.1, Q5.1 (G), R27.2, RN1.4
unnamed: C7.1, Q6.1 (G), R20.2, RN1.2
unnamed: C18.1, Q7.1 (G), R37.2, RN2.2
unnamed: C11.1, Q8.1 (G), R22.2, RN1.6
unnamed: C19.1, Q9.1 (G), R38.2, RN2.6, RN2.7, RN2.8
unnamed: C17.1, Q10.1 (G), R42.2, RN2.4

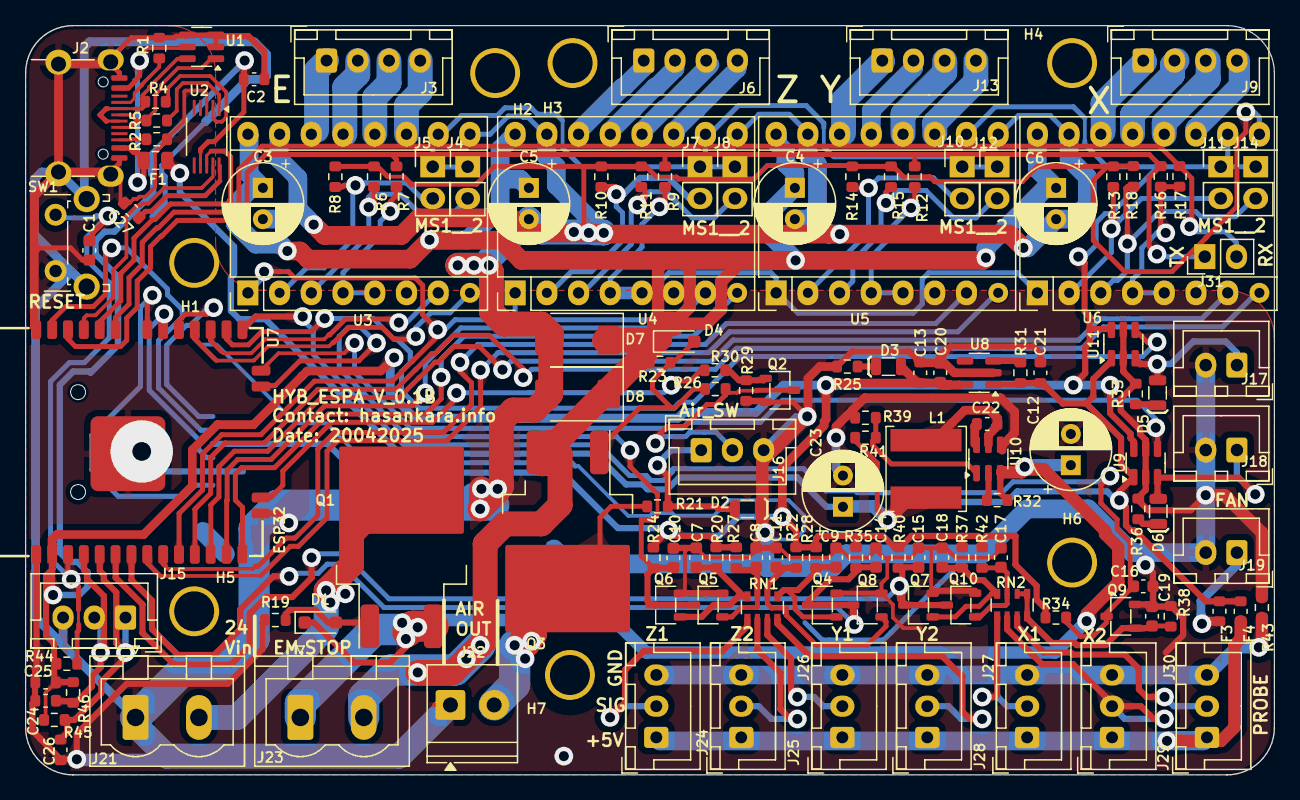
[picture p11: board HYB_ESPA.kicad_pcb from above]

Board: 2 copper layers, 100.0 x 60.0 mm, 146 parts (1 on the bottom side), 103 nets.

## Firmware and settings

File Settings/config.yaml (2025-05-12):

name: "4 stepper motors can be connected, CNC controller."
board: "HYB_ESPA"
meta: 2025-04-20 CNC
stepping:
  engine: RMT
  idle_ms: 255
  dir_delay_us: 2
  pulse_us: 6
  disable_delay_us: 2
  segments: 12

kinematics:
  cartesian:

uart1:
  txd_pin: gpio.22
  rxd_pin: gpio.21
  baud: 115200
  mode: 8N1

axes:
  shared_stepper_disable_pin: gpio.25:high
  homing_runs: 2
  x:
    steps_per_mm: 400
    max_rate_mm_per_min: 2400.0
    acceleration_mm_per_sec2: 100.0
    max_travel_mm: 310.0
    soft_limits: true
    homing:
      cycle: 2
      positive_direction: true
      mpos_mm: 310.0
      feed_mm_per_min: 200
      seek_mm_per_min: 1000
      settle_ms: 200
      seek_scaler: 1.0
      feed_scaler: 1.0
    motor0:
      limit_all_pin: gpio.34:low
      hard_limits: true
      pulloff_mm: 0.5
      # x stepper slave mode, use z stepper parameters
      tmc_2208:
        step_pin: gpio.27
        direction_pin: gpio.26:low

        uart_num: 1
        addr: 0
        #en_spreadcycle : true
        r_sense_ohms: 0.110
        run_amps: 1.0
        hold_amps: 0.5
        microsteps: 16
        stallguard: 1
        stallguard_debug: false
        toff_disable: 0
        toff_stealthchop: 5
        toff_coolstep: 3
        run_mode: CoolStep
        homing_mode: CoolStep
        use_enable: false
        disable_pin: NO_PIN

  y:
    steps_per_mm: 400
    max_rate_mm_per_min: 2400.0
    acceleration_mm_per_sec2: 100.0
    max_travel_mm: 215.0
    soft_limits: true
    homing:
      cycle: 2
      positive_direction: true
      mpos_mm: 215.000
      feed_mm_per_min: 200.0
      seek_mm_per_min: 1000.0
      settle_ms: 200
      seek_scaler: 1.0
      feed_scaler: 1.0

    motor0:
      limit_all_pin: gpio.35:low
      hard_limits: true
      pulloff_mm: 0.5
      # y stepper slave mode, use z stepper parameters
      tmc_2208:
        step_pin: gpio.33
        direction_pin: gpio.32:high

        uart_num: 1
        addr: 0
        #en_spreadcycle : true
        r_sense_ohms: 0.110
        run_amps: 1.0
        hold_amps: 0.5
        microsteps: 16
        stallguard: 1
        stallguard_debug: false
        toff_disable: 0
        toff_stealthchop: 5
        toff_coolstep: 3
        run_mode: CoolStep
        homing_mode: CoolStep
        use_enable: false
        disable_pin: NO_PIN

  z:
    steps_per_mm: 400
    max_rate_mm_per_min: 2400.0
    acceleration_mm_per_sec2: 100.0
    max_travel_mm: 85.0
    soft_limits: true
    homing:
      cycle: 1
      positive_direction: true
      mpos_mm: 85.0
      feed_mm_per_min: 200.0
      seek_mm_per_min: 1000.0
      settle_ms: 200
      seek_scaler: 1.0
      feed_scaler: 1.0
    motor0:
      limit_all_pin: gpio.15:low
      #limit_neg_pin: gpio.15
      hard_limits: true
      pulloff_mm: 0.5
      tmc_2208:
        step_pin: gpio.14
        direction_pin: gpio.12:high

        uart_num: 1
        addr: 0
        #en_spreadcycle : true
        r_sense_ohms: 0.110
        run_amps: 1.0
        hold_amps: 0.5
        microsteps: 16
        stallguard: 1
        stallguard_debug: false
        toff_disable: 0
        toff_stealthchop: 5
        toff_coolstep: 3
        run_mode: CoolStep
        homing_mode: CoolStep
        use_enable: false
        disable_pin: NO_PIN

pwm:
  pwm_hz: 1000
  direction_pin: NO_PIN
  output_pin: gpio.2
  enable_pin: gpio.13
  disable_with_s0: true
  s0_with_disable: true
  spinup_ms: 1000
  spindown_ms: 1000
  tool_num: 0
  speed_map: 0=0.000% 1000=1.000% 30000=97.000%
  off_on_alarm: false

coolant:
  #flood_pin: gpio.13
  #mist_pin: gpio.13
  delay_ms: 1000

spi:
  miso_pin: gpio.19
  mosi_pin: gpio.23
  sck_pin: gpio.18
  

sdcard:
  cs_pin: gpio.05
  card_detect_pin: NO_PIN

start:
  must_home: false
  deactivate_parking: false
  check_limits: false

probe:
  pin: gpio.0:low
  check_mode_start: false

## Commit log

2025-05-12 Fixed component name positions in, Top silk, F. Fab, and ibom, files.
    [HYB_ESPA.kicad_pcb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]
2025-05-12 Updated Pwm speed map in Settings dir config.yaml file.
